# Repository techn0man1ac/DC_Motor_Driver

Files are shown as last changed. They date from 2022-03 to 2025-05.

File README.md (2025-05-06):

# BJT/MOSFET DC Motor Driver

Fully isolated DC driver for collector motors 10 Amps:

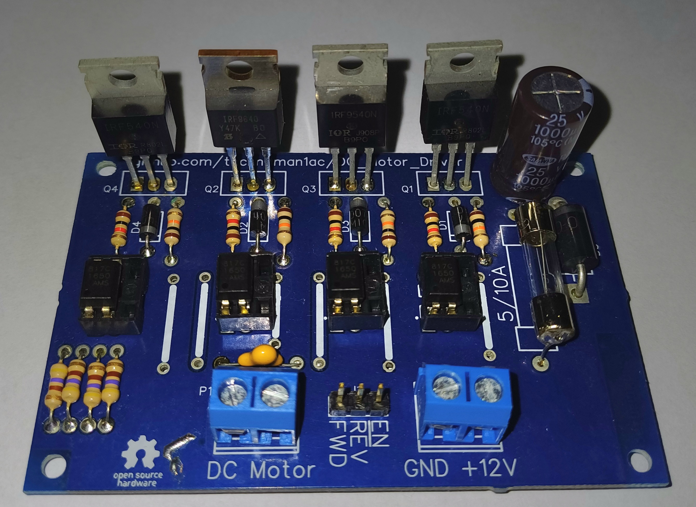
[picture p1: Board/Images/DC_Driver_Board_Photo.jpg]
Real board photo


Specifications:
- Vin 10..20 V;
- PWM(EN pin, active LOW level) up to 1 KHz(with PC817 optocoupler) or 10 KHz(with PC123);
- Current 2..4 A(Q1, Q4 - TIP122 / Q2, Q3 - TIP127, FU1 5A), 7..10 A(Q10, Q6 - IRF4905 / Q9, Q5 -IRF3205, FU1 10A).

# Video demonstration

https://www.youtube.com/shorts/6-JHy-ymlhs

# Schematic

Schematic(BJT or MOSFET):

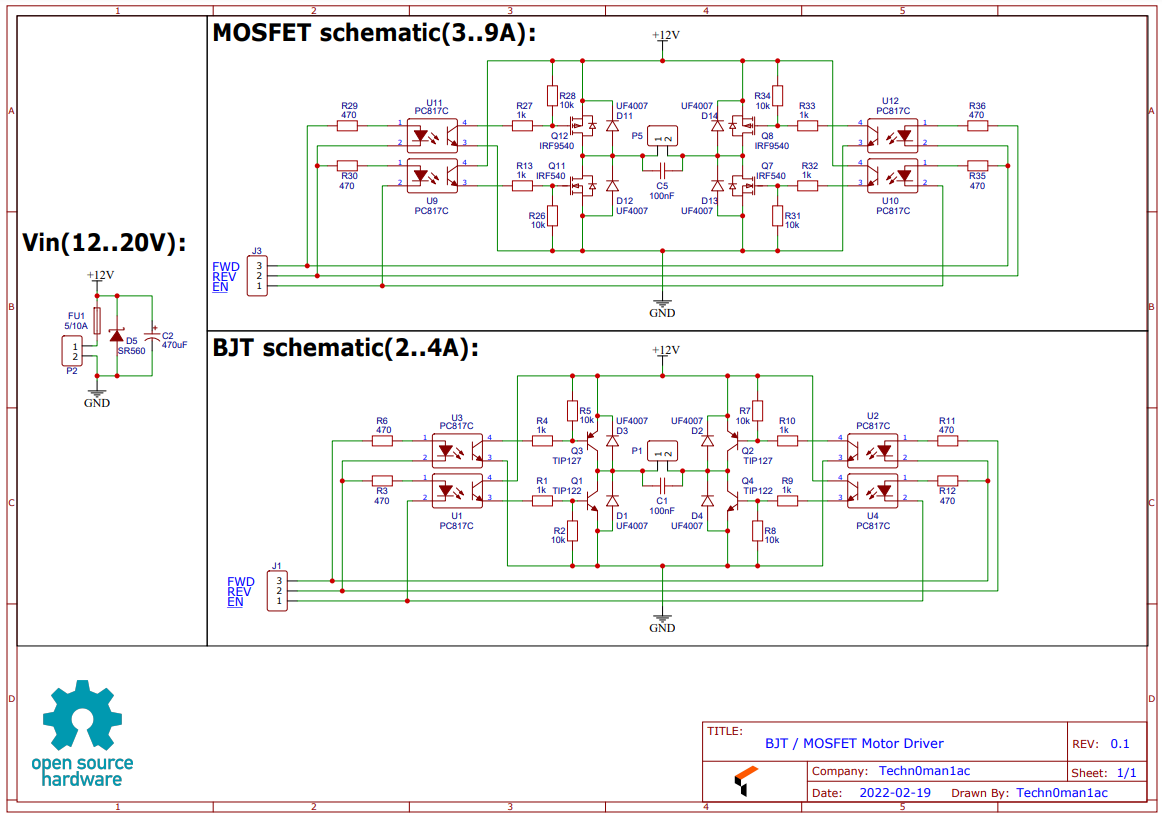
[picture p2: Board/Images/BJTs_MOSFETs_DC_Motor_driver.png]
Schematic BJTs/MOSFETs_DC_Motor_driver

  
# PCB

PCB have are 800x522mm, one(blue) or two Layers:

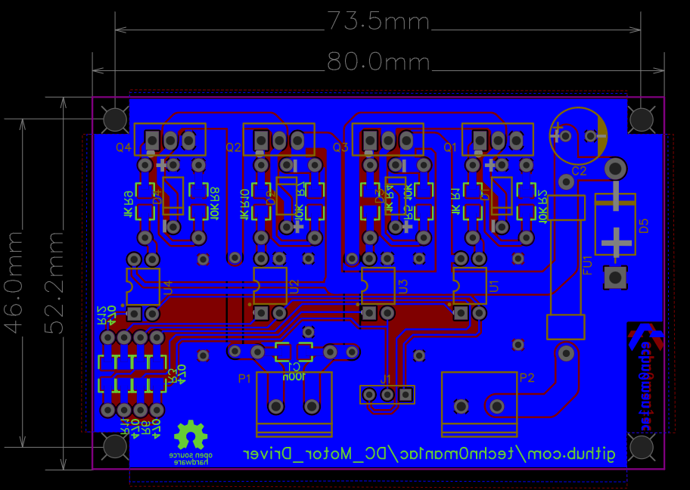
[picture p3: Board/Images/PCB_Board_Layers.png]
PCB_Board_Layers


The minimum track size is 0.254 mm.

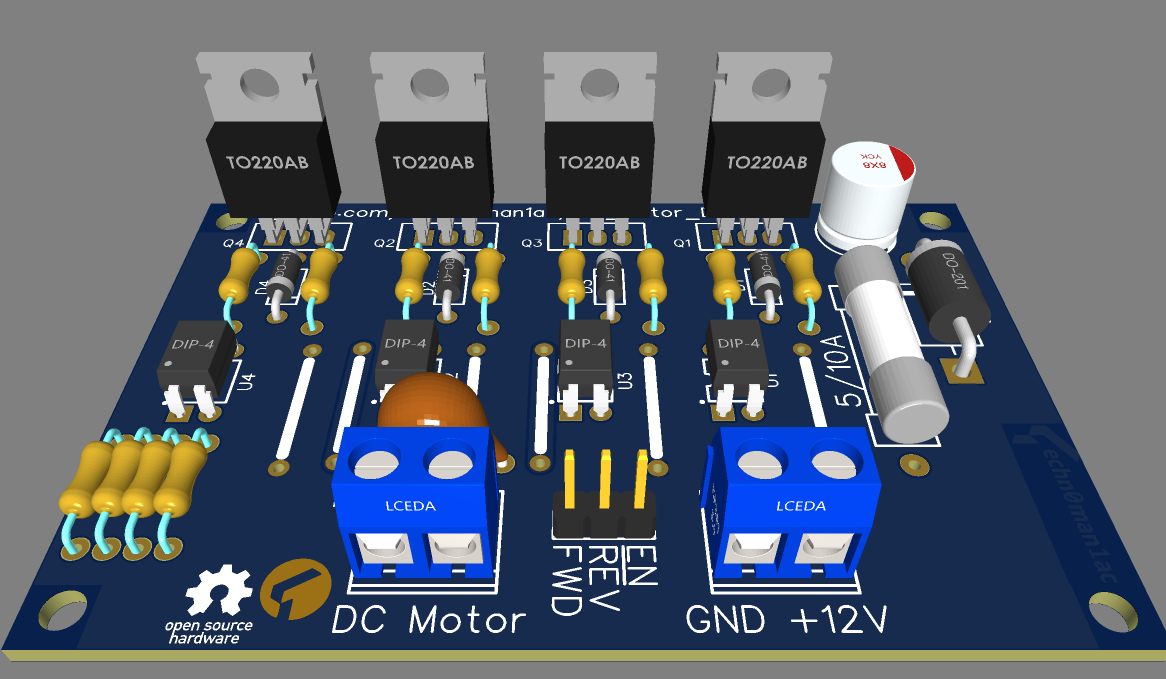
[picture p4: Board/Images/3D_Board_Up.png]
3D_Board


3D model file:

https://github.com/techn0man1ac/DC_Motor_Driver/tree/main/Board/3D%20model/OBJ_PCB_BJT

PCB and schematic page:

https://oshwlab.com/raznie.podelki/bjt_motordriver

Here gerbers files:

https://github.com/techn0man1ac/DC_Motor_Drive/tree/main/Board/Gerbers

Project have are Proteus 8.11 model:

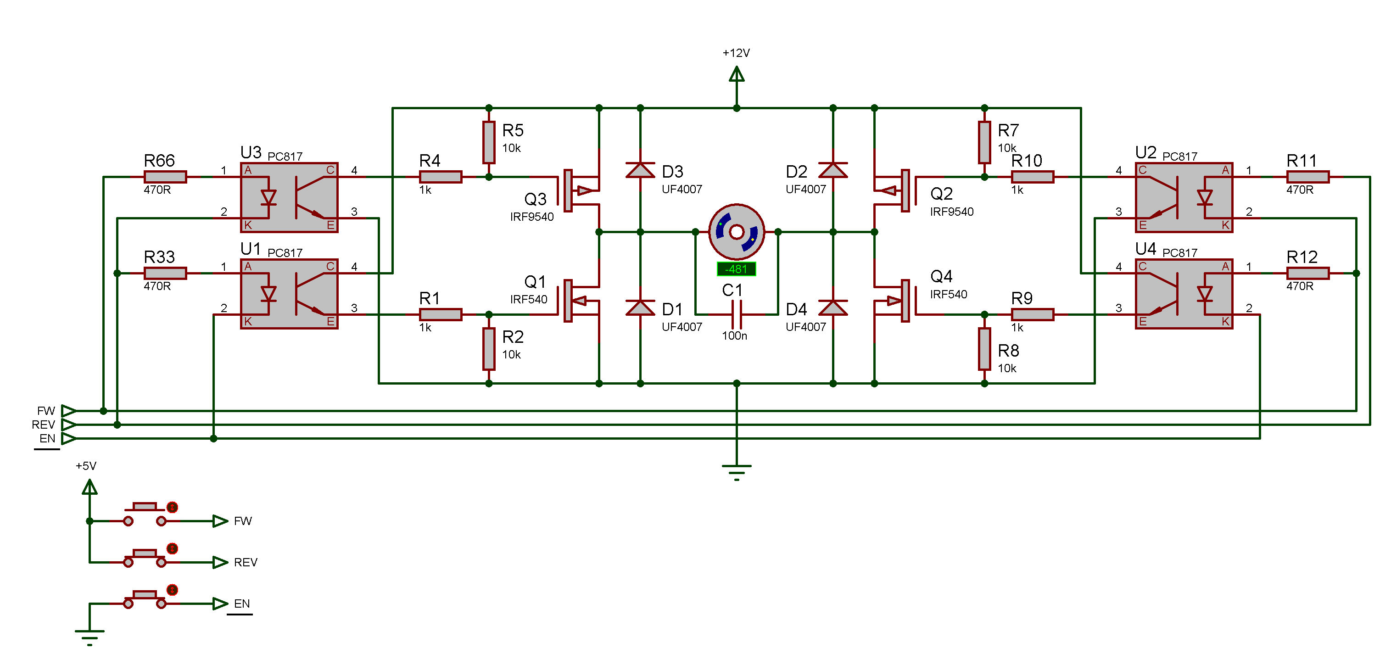
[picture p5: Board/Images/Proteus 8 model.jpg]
Proteus 8.11 model


Arduino code:

https://github.com/techn0man1ac/DC_Motor_Driver/tree/main/DC_Motor_Driver

The idea of the circuitry from here:

https://itectec.com/electrical/electronic-bjh-h-bridge-going-in-reverse-but-not-forward-ll-transistor-overheating/

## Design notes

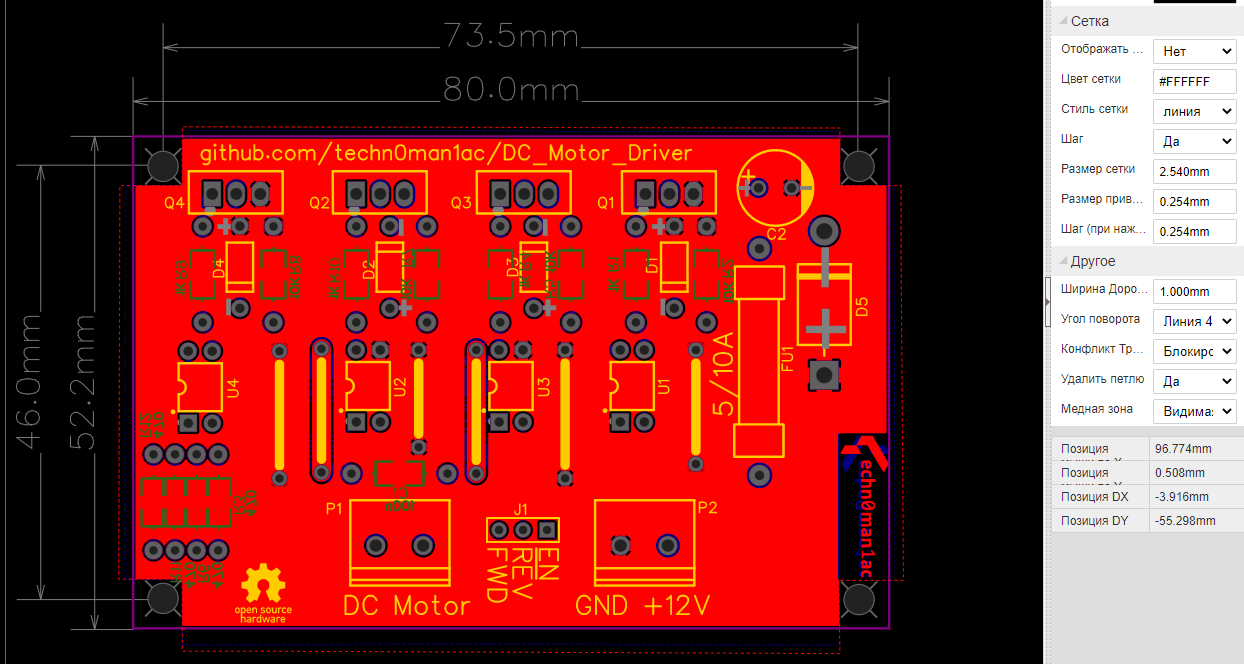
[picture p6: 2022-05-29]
Board/Images/PCB_Board_Bottom_Layers.png

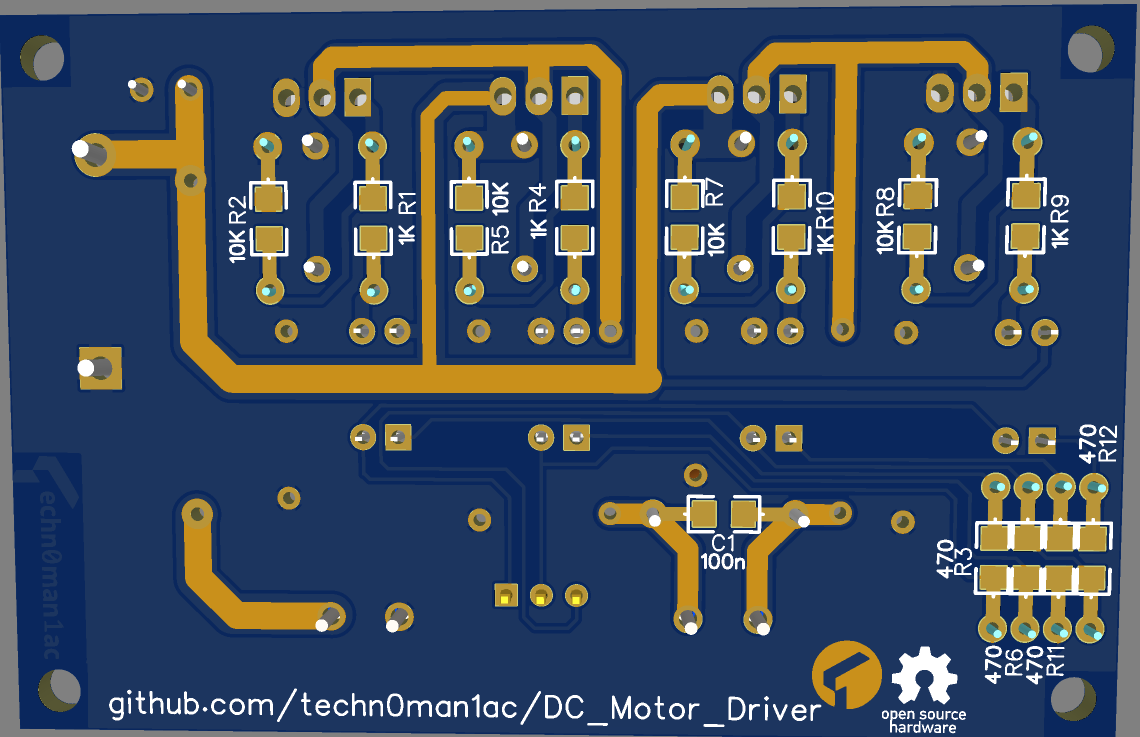
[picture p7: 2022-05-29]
Board/Images/3D_Board_Bottom.png

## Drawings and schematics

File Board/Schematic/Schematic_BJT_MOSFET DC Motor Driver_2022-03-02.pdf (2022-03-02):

# MOSFET schematic(3..9A):

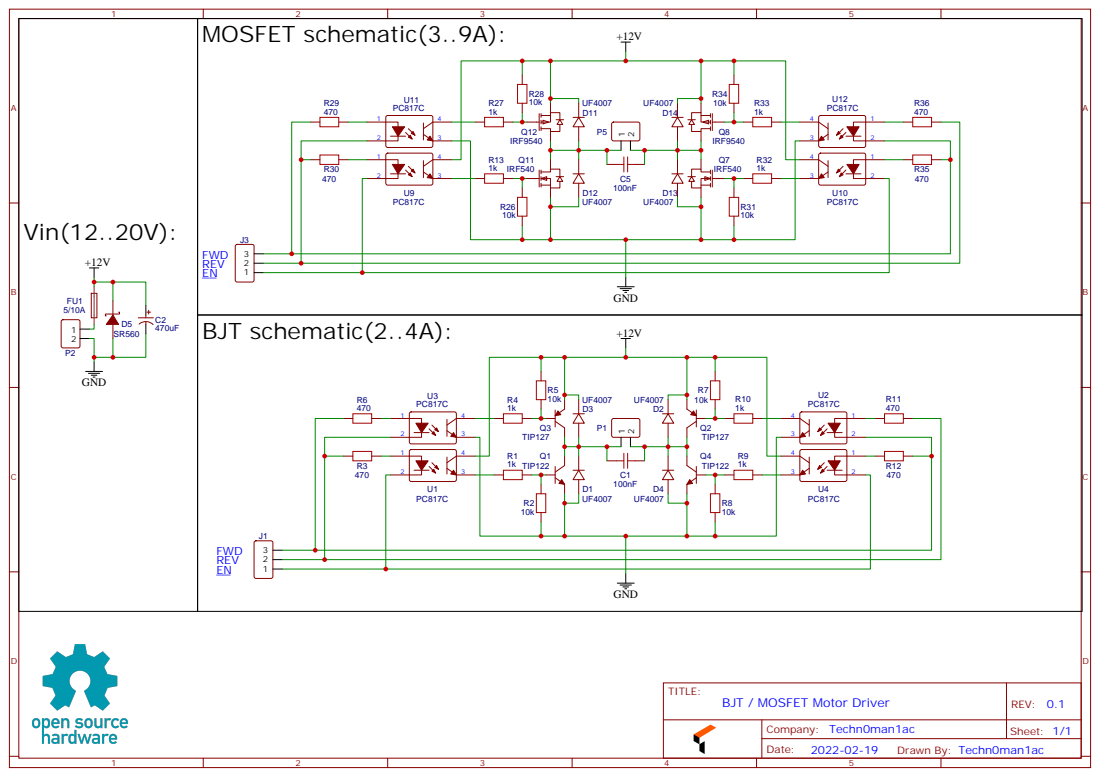
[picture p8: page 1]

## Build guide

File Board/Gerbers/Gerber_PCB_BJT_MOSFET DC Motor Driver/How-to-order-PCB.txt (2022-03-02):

How to Order PCB

Please refer to:
https://docs.easyeda.com/en/PCB/Order-PCB

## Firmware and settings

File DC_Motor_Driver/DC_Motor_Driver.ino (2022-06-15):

/*
  DC_Motor_Driver
  https://github.com/techn0man1ac/DC_Motor_Driver
  by Techn0man1ac Labs, 2022
*/

#define EN0 9
#define REV0 7
#define FW0 8

#define EN1 10
#define REV1 5
#define FW1 6

int RightMotor = 0; 
int LeftMotor = 0;

void setup() {
  pinMode(EN0, OUTPUT);
  digitalWrite(EN0, HIGH);
  pinMode(EN1, OUTPUT);
  digitalWrite(EN1, HIGH);
  pinMode(REV0, OUTPUT);
  digitalWrite(REV0, LOW);
  pinMode(REV1, OUTPUT);
  digitalWrite(REV1, LOW);
  pinMode(FW0, OUTPUT);
  digitalWrite(FW0, LOW);
  pinMode(FW1, OUTPUT);
  digitalWrite(FW1, LOW);


  MtrsSpdSet(64, -64);
  delay(500);
  MtrsSpdSet(-64, 64);
  delay(500);
  MtrsSpdSet(0, 0);

  Serial.begin(115200);
  Serial.setTimeout(5);  

  Serial.println(" Start "); 
}

void loop() {
  if (Serial.available() > 0) { //Если в буфере UART'а есть что-то
    char data = Serial.read();
    if (data == 'r') {
      RightMotor = Serial.parseInt();
    }
    if (data == 'l') {
      LeftMotor = Serial.parseInt();
    }
  }

  MtrsSpdSet(RightMotor, LeftMotor); //r -255..255, l -255..255
}

void MtrsSpdSet(int rMotor, int lMotor) {
  if (rMotor > 0) {
    rMotor = 255 - rMotor; // Inverse 255-245 -> 10, 255-100 -> 155
    digitalWrite(REV0, HIGH);
    digitalWrite(FW0, LOW);
  } else if (rMotor == 0) {
    digitalWrite(REV0, LOW);
    digitalWrite(FW0, LOW);
  } else if (rMotor < 0) {
    rMotor = abs(rMotor);
    rMotor = 255 - rMotor;
    digitalWrite(REV0, LOW);
    digitalWrite(FW0, HIGH);
  }

  if (lMotor > 0) {
    lMotor = 255 - lMotor;
    digitalWrite(REV1, HIGH);
    digitalWrite(FW1, LOW);
  } else if (lMotor == 0) {
    digitalWrite(REV1, LOW);
    digitalWrite(FW1, LOW);
  } else if (lMotor < 0) {
    lMotor = abs(lMotor);
    lMotor = 255 - lMotor;
    digitalWrite(REV1, LOW);
    digitalWrite(FW1, HIGH);
  }

  analogWrite(EN0, rMotor);
  analogWrite(EN1, lMotor);
}

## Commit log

2022-03-02 Change001
    Add project files
    [Drill_NPTH_Through.DRL, Drill_PTH_Through.DRL, Gerber_BoardOutlineLayer.GKO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]
2022-05-29 Delete Board directory
    Some errors
    [Drill_NPTH_Through.DRL, Drill_PTH_Through.DRL, Gerber_BoardOutlineLayer.GKO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]
2022-05-29 Change 003
    On PCB must be R8 - 10K, R8 - 1K. It's my false.
    [Drill_NPTH_Through.DRL, Drill_PTH_Through.DRL, Gerber_BoardOutlineLayer.GKO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]
2022-06-15 Change 004
    Add Arduino code example
2022-06-15 Change 005
    Add Arduino code for 2 drivers
2023-08-06 Change №005
    Add real board photo
2023-08-06 Change №006
    Add 3D model files
2023-08-06 Change №006
    Change structures
2023-09-03 Change №007
    Add video link
2025-05-06 Change#008
    Add new powerful transistors
